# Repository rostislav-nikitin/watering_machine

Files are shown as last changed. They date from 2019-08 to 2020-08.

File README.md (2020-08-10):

# Watering machine

Watering machine is a device that control a watering of the garden. This particular machine provides sequential zones watering. This was made to avoid low watering pressure that can happens in case of the parallel mode zone watering.

This device is a control unit with outputs to the external valves - one per watering zone.

<!--![picture](https://cloud.dynacore.systems/apps/files_sharing/publicpreview/L8qHpaeza94Mbzw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 "") -->


## Modes
The device is designed to work in a two primary modes.

**Normal watering mode**

Used for the regular day-by-day watering. Each zone watering time interval set by the particular zone settings.

**Service mode**

Used for the system blowing before the coservation.
Usually in this mode pump provides an air instead of water. In this case switching to the next zone should be done manually. Through the control button/external input instead of zones watering interval time settings.

According to this, some of button has a different functions depends on the current mode and device state.

## Device logical structure
* [PCB 3D view](#pcb-3d-view "PCB 3D view")
* [Inputs](#Inputs "Inputs")
    * [Power inputs](#power-inputs "Power inputs")
	    * [Main power input](#main-power-input "Main power input")
		    * [Internal low-voltage circuits powering](#internal-low-voltage-circuits-powering "Internal low-voltage circuits powering")
            * [Valves powering](#valves-powering "Valves powering")
        * [Batteries bay](#batteries-bay "Batteries bay")
    * [Logical inputs](#logical-inputs "Logical inputs")
	    * [Control buttons](#control-buttons "Control buttons")
	    * [24 hours internal timer](#24-hours-internal-timer "24 hours internal timer")
	    * [External inputs](#external-inputs)
	        * [External TTL-levels input](#external-ttl-levels-input "External TTL-levels input")
		    * [External rain sensor input](#external-rain-sensor-input "External rain sensor input")
* [Outputs](#outputs "Outputs")
	* [State indicators](#state-indicators "State indicators")
	* [Valves outputs](#valves-outputs "Valves outputs")
	* [Cascading output (not implemented yet)](#cascading-output "Cascading output (not implemented yet)")

## PCB 3D view

<!-- ![picture](https://cloud.dynacore.systems/apps/files_sharing/publicpreview/zAkpRHqrjZDFHtE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 "") -->

	
## Inputs

### Power inputs

#### Main power input

This device can be powered by the 9-36 VAC / 500 mA+ power supply.
Power supply characteristics should be calculated by a next formula:

Power supply voltage = valve voltage. Accepted range: [9 VAC - 36 VAC].

Power supply minimal current = 500 mA (internal circuits) + valve maximal current. Accepterd range: [500 mA - 2 A].

##### Internal low-voltage circuits powering
To power input low-voltage circuits was used primary power supply through current rectification and stabilisation. There is +5 VDC powering used for the low-voltage TTL circuits.
* U = +5 VDC (+/- 5%)
* I <= 700 mA

##### Valves powering
Valves solenoids are powering directly from the [main power input](#main-power-input "Main power input") through triacs without any stabilization or transformation.

#### Batteries bay
Battery powering is consists of the battery bay & controller which control charge level/charge batteries. It powers only chips required to run internal time and store device 24 hours timer state. Because they should be invariant for the external power outages.
Ther was used battery bay for 2x18650 battries. Bacause each battery voltage is 3.8-4.2 VDC. And if they are connected sequetely then they provides ~8 VDC voltage. Which is enough to provide +5 VDC after the stabilization.

### Logical inputs

#### Control buttons
Control buttons should be used to set the current watering mode, zone watering time intervals and change the device state - start, stop watering, switch to the next zone manually.

##### Mode switch button

This button toggle normal watering mode / service mode.

##### Start/Stop/Next button

_In the normal watering mode_

In this mode Start/Stop/Next button works in a Start/Stop toggle mode. When device not in a progress state and rain sensor circuit is disonnected then it start watering. Otherwise if device is in progress then stop.

_In the serivce mode_

In this mode Start/Stop/Next button works in a Start->Next->Stop mode. When watering is stopped then this button starts it in case rain sensor circuit is disconnected. On the next push it switch watering zone to the next one. On push when the last zone is in progress it stops the watering.

##### Timer On/Off switch button

This button toggle [24 hours internal timer](#24-hours-internal-timer "24 hours internal timer") on/off.

##### Zone watering time interwal switch

Each zone watering time can be set with a 3 minutes percision.

There are 2 x 5-position sliding switches per zone. One for the rough setup and one for the fine setup. The total zone watering time interval is a sum of rough and fine values.

_Rough setup 5-position sliding switch_

Positions: [1] - 0 minutes, [2] - 15 minutes, [3] - 30 minutes, [4] - 45 minutes, [5] - 60 minutes

_Fine setup 5-position sliding switch_

Positions: [1] - 0 minutes, [2] - 3 minutes, [3] - 6 minutes, [4] - 9 minutes, [5] - 12 minutes

Example: If rough switch in a position [3] (30 minutes) and fine switch in a position [4] (9 minutes) then zone time interval is equal to the  30 minutes + 9 minutes = 39 minutes

#### 24 hours internal timer
24 hours internal timer is used to start watering each 24 hours with everyday recuring.

Timer On/Off button toggle timer function.

##### Watering start time setup
Watering start time could be setup only in normal watering model. This can be made through a manual start watering by the pressing a start/stop/next or by external TTL-levels input high signal. And after the 24 hours it will starts watering again if device is not in a progress state and rain sensor circuit is disconnected.

#### External inputs

##### External TTL-levels input
The external TTL-levels input behaviour is a same as [Start/Stop/Next button](#start/stop/next-button "Start/Stop/Next button") behaviour. Each high TTL level toggle watering state depends on the current mode and the rain sensor circuit conection state.

##### External rain sensor input
It can be used to connect external rain sensor. Rain sensor shold connect both connector pins on rain begins and disconnect on rain ends. When pins are connected then watering is blocking with a maximal priority - no one signal can start watering.
If it connects pins when watering was is in progress then watering stops. And starts only when next start signal comes in case if rain sensor connector pins will be disconnected. 

## Outputs

### State indicators
* Power indicator: 
    * Off if device powered off
    * On if device is powered on
* Mode indicator: 
    * Off if device is in normal watering mode
    * On if device is in service mode
* In progress indicator:
    * Off if device in suspend mode (waiting for the start watering signal)
    * On if watering is in progress
* Zone watering in progress indicator. Each zone has own it's one:
    * Off if a current zone watering not is in progress state
    * On if a current zone watering is in progress state
* Rain indicator:
    * Off if rain sensor circuit is disconnected
    * On if rain sensor circuit is connected
* Change battery indicator:
    * Off if battery in a good state
    * Flashes if battery is corrupted and need replacement

### Valves outputs
There are ouptuts with [valves powering](#valves-powering "Valves powering"). At the moment only one output is active, according to the current watering zone.

### Cascading output
On last zone watering finish there is raises short high-level TTL impulse to cascade next watering device in watering devices sequence.

## Links
Watering machine intro and description on my YouTube channel:

Watering machine (https://www.youtube.com/playlist?list=PLeO-sYwJtKn6DI-ZfQoCn5SV4Xy-Knc86 "Watering machine")

## Contacts
e-mail: rostislav.nikitin@gmail.com

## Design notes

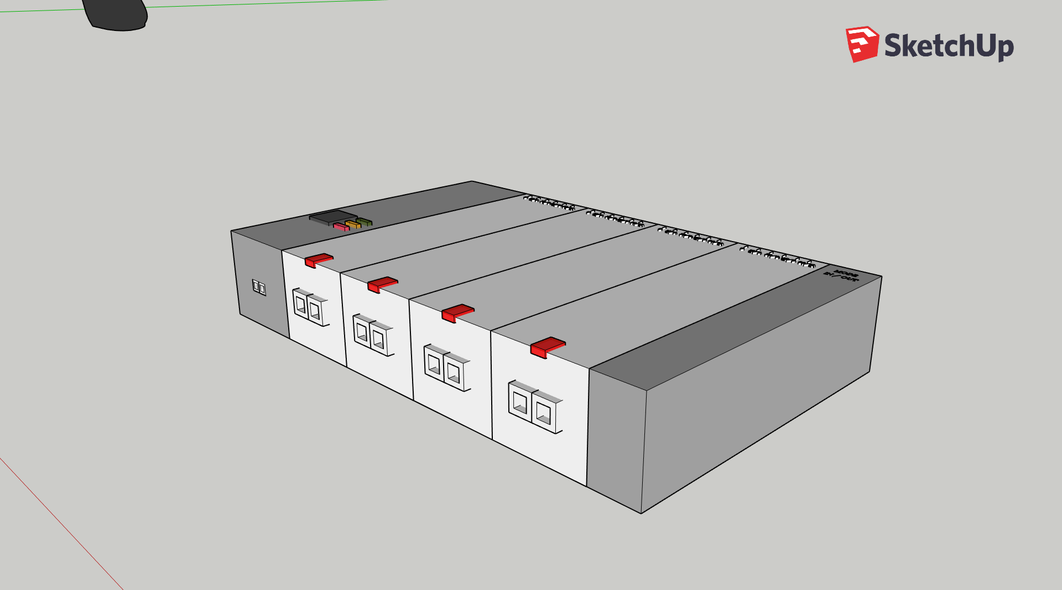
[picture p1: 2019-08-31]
src/case_design/sketches/front-top-right.png

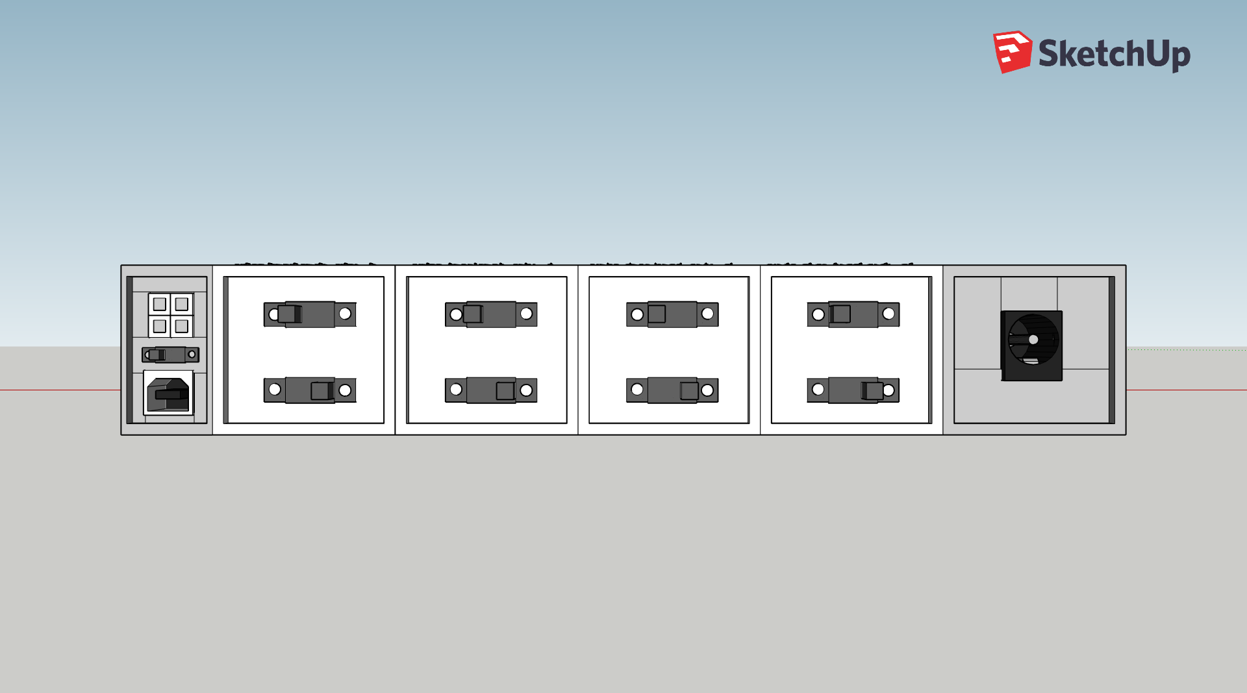
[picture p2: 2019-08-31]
src/case_design/sketches/back.png

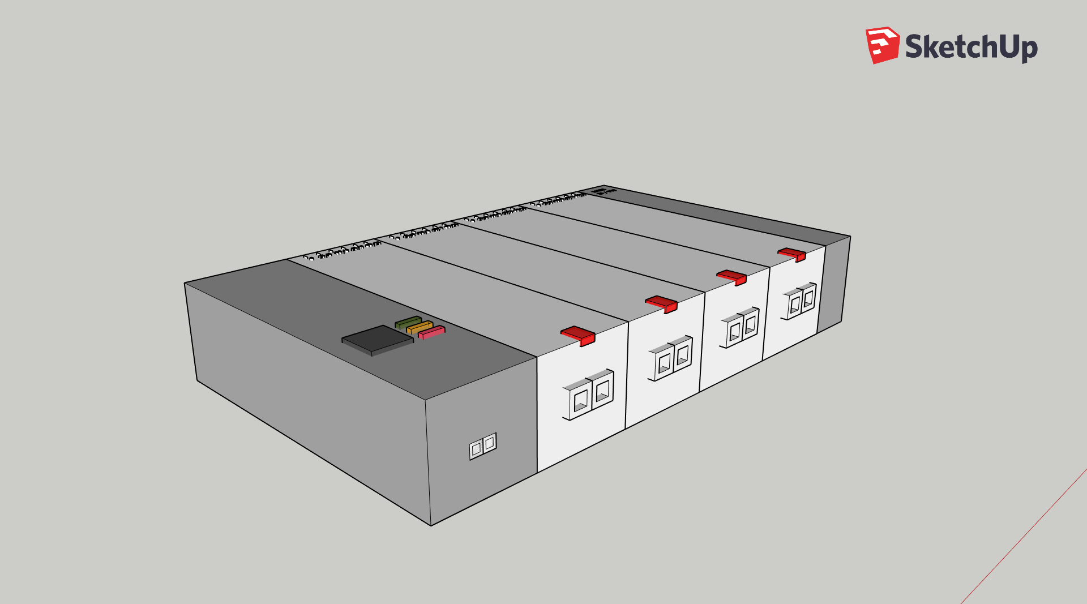
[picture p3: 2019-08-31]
src/case_design/sketches/front-top-left.png

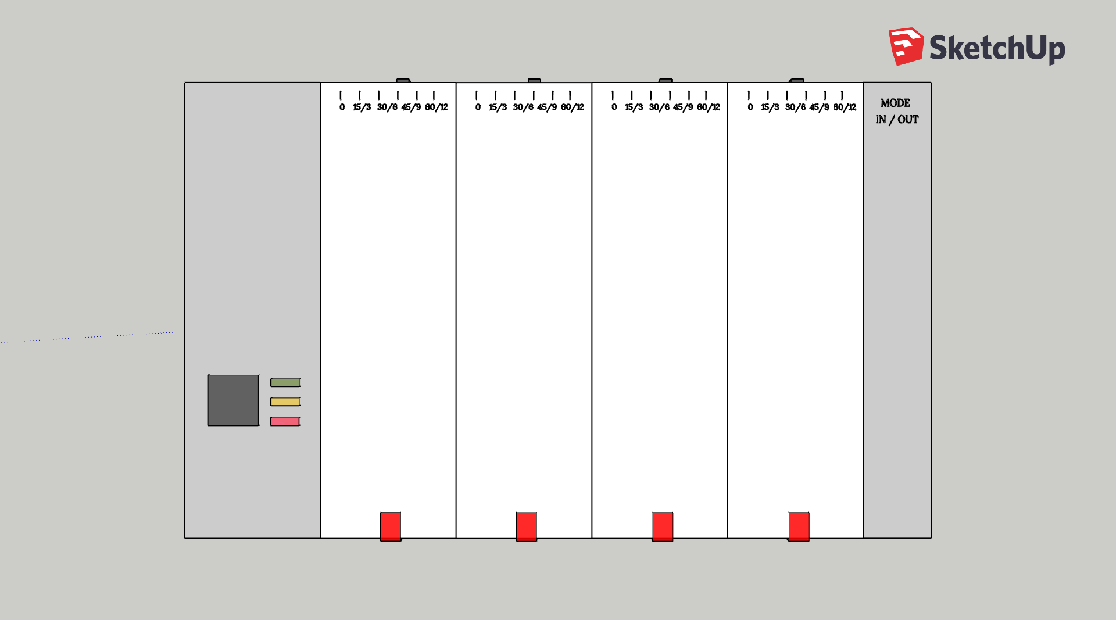
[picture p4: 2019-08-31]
src/case_design/sketches/top.png

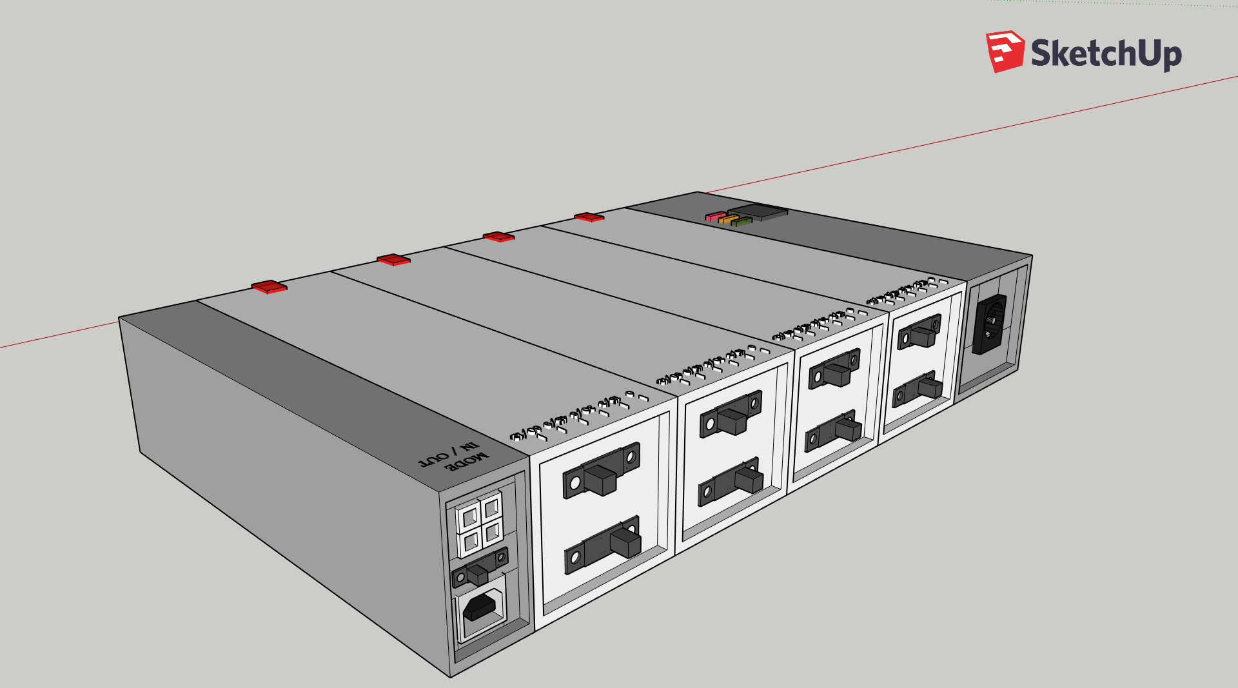
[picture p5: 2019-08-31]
src/case_design/sketches/back-top-left.png

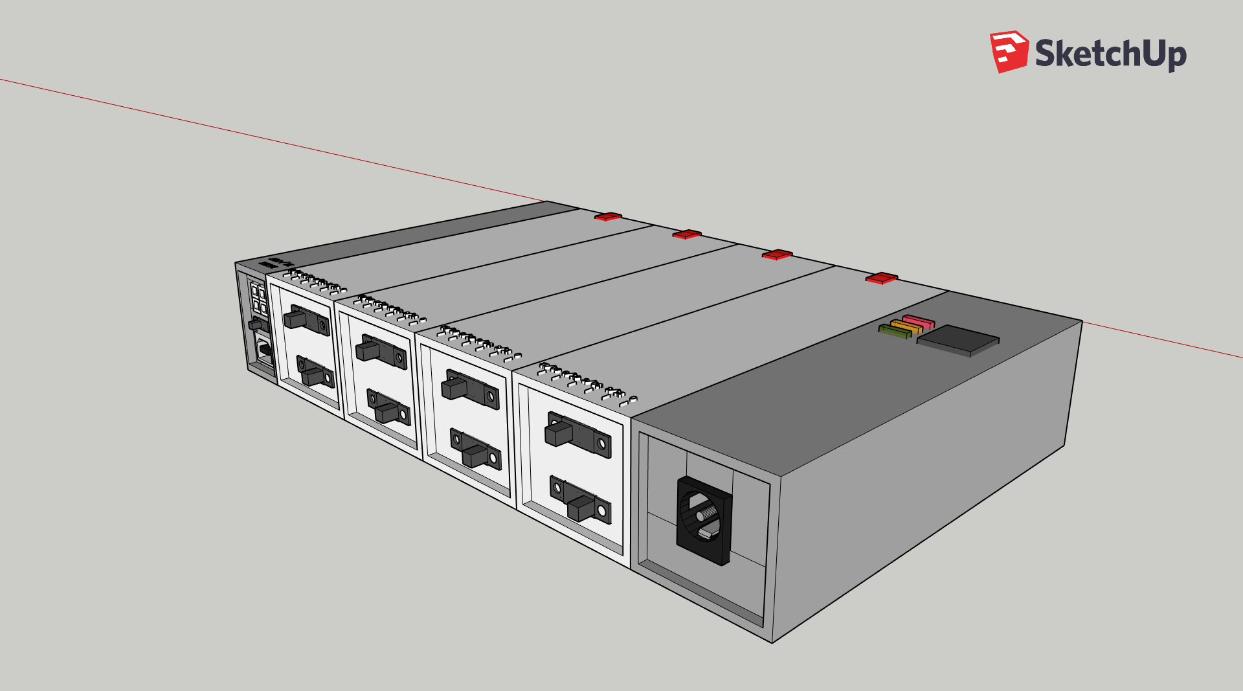
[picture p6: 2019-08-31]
src/case_design/sketches/back-top-right.png

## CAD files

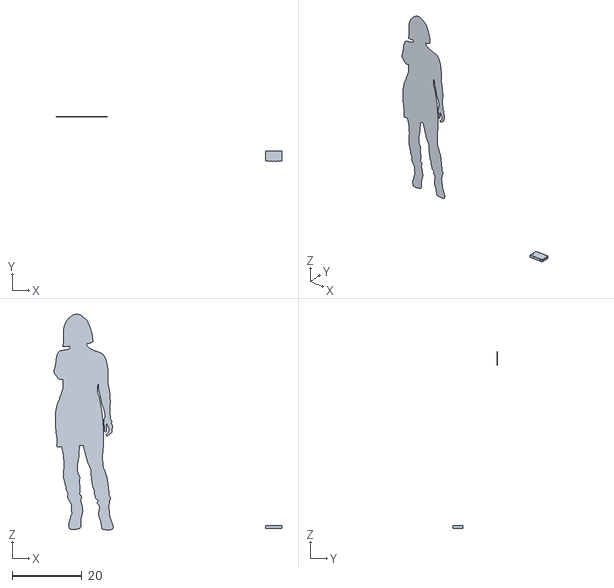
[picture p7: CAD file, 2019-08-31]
src/case_design/case_design.stl
65.6 x 12.9 x 62.1

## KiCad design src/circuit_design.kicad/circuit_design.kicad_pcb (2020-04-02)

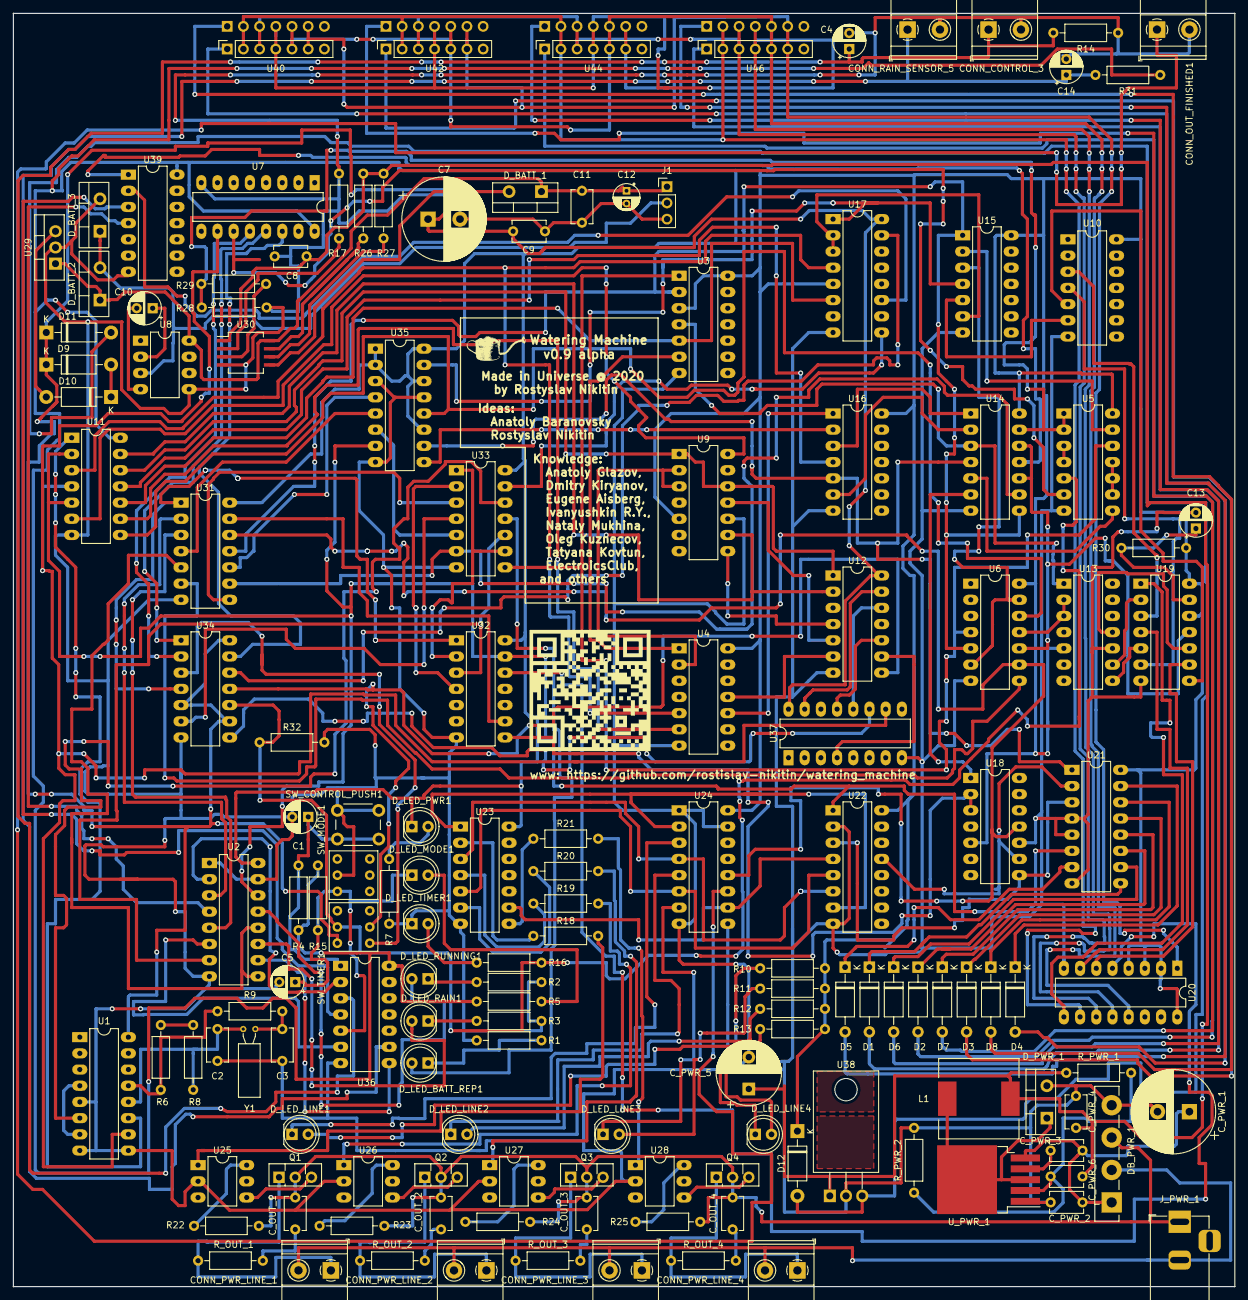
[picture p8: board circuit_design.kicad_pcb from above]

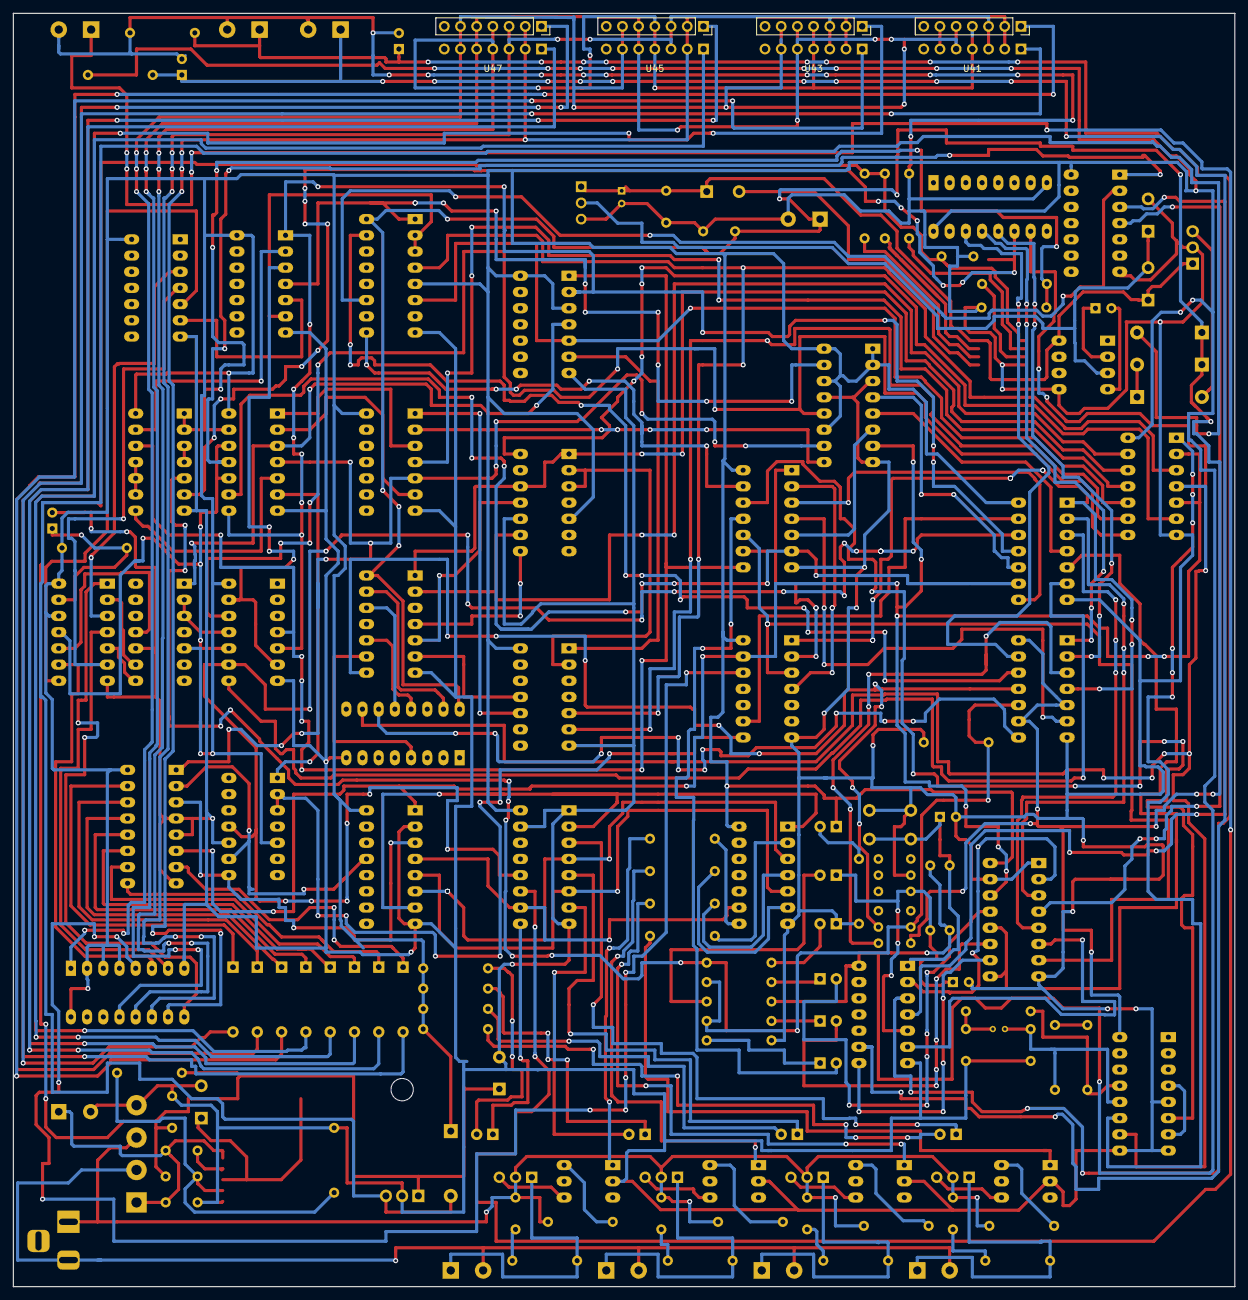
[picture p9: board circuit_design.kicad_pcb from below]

Board: 2 copper layers, 191.5 x 199.6 mm, 154 parts (4 on the bottom side), 186 nets.

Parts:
C1, C4, C5, C13, C14: 100uF; CP_Radial_D5.0mm_P2.50mm
C2: 62pF; C_Disc_D5.1mm_W3.2mm_P5.00mm
C3: 22pF; C_Disc_D5.1mm_W3.2mm_P5.00mm
C7: 1000uF; CP_Radial_D13.0mm_P5.00mm
C8, C11: 100nF; C_Disc_D5.1mm_W3.2mm_P5.00mm
C9: 105; C_Disc_D5.1mm_W3.2mm_P5.00mm
C10: 10uF/16V; CP_Radial_D5.0mm_P2.50mm
C12: 22uF/16V; CP_Radial_D4.0mm_P2.00mm
CONN_CONTROL_3: Conn_01x02_Male; TerminalBlock_Phoenix_MKDS-1,5-2-5.08_1x02_P5.08mm_Horizont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
CONN_OUT_FINISHED1: Conn_01x02_Male; TerminalBlock_Phoenix_MKDS-1,5-2-5.08_1x02_P5.08mm_Horizont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
CONN_PWR_LINE_1, CONN_PWR_LINE_2, CONN_PWR_LINE_3, CONN_PWR_LINE_4: Conn_01x02_Male; TerminalBlock_Phoenix_MKDS-1,5-2-5.08_1x02_P5.08mm_Horizont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
CONN_RAIN_SENSOR_5: Conn_01x02_Male; TerminalBlock_Phoenix_MKDS-1,5-2-5.08_1x02_P5.08mm_Horizont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
C_OUT_1, C_OUT_2, C_OUT_3, C_OUT_4: 103; C_Disc_D5.1mm_W3.2mm_P5.00mm
C_PWR_1: 1000 uF/50V; CP_Radial_D13.0mm_P5.00mm
C_PWR_2, C_PWR_3, C_PWR_4: 105; C_Disc_D5.1mm_W3.2mm_P5.00mm
C_PWR_5: 330 uF/50V; CP_Radial_D10.0mm_P5.00mm
C_PWR_6: 333; C_Disc_D5.1mm_W3.2mm_P5.00mm
D1, D2, D3, D4, D5, D6, D7, D8: 1N5817; D_A-405_P10.16mm_Horizontal
D9, D11, D12: 1N4007; D_DO-41_SOD81_P10.16mm_Horizontal
D10: 1N5817; D_DO-41_SOD81_P10.16mm_Horizontal
DB_PWR_1: RS207; Diode_Bridge_Vishay_GBL
D_BATT_1, D_BATT_2, D_BATT_3: SS24T3G; TO-220-2_Vertical
D_LED_BATT_REP1: LED; LED_D5.0mm
D_LED_LINE1, D_LED_LINE2, D_LED_LINE3, D_LED_LINE4: LED; LED_D5.0mm
D_LED_MODE1: LED; LED_D5.0mm
D_LED_PWR1: LED; LED_D5.0mm
D_LED_RAIN1: LED; LED_D5.0mm
D_LED_RUNNING1: LED; LED_D5.0mm
D_LED_TIMER1: LED; LED_D5.0mm
D_PWR_1: MBR745; TO-220-2_Vertical
J1: CONN_BAT; PinHeader_1x03_P2.54mm_Vertical
J_PWR_1: Barrel_Jack; BarrelJack_Horizontal
L1: 47 uH/5A; L_12x12mm_H6mm
Q1, Q2, Q3, Q4: BT134-600E; TO-126-3_Vertical
R1: 200; R_Axial_DIN0207_L6.3mm_D2.5mm_P10.16mm_Horizontal
R2, R3, R5, R7, R10, R11, R12, R13: 270Ohm; R_Axial_DIN0207_L6.3mm_D2.5mm_P10.16mm_Horizontal
R4, R14, R15, R22, R23, R24, R25, R31: 1KOhm; R_Axial_DIN0207_L6.3mm_D2.5mm_P10.16mm_Horizontal
R6, R8: 10MOhm; R_Axial_DIN0207_L6.3mm_D2.5mm_P10.16mm_Horizontal
R9: 510KOhm; R_Axial_DIN0207_L6.3mm_D2.5mm_P10.16mm_Horizontal
R16: 270; R_Axial_DIN0207_L6.3mm_D2.5mm_P10.16mm_Horizontal
R17, R27, R30: 10K; R_Axial_DIN0207_L6.3mm_D2.5mm_P10.16mm_Horizontal
R18, R19, R20, R21: 100 Ohm; R_Axial_DIN0207_L6.3mm_D2.5mm_P10.16mm_Horizontal
R26: 0.5R; R_Axial_DIN0207_L6.3mm_D2.5mm_P10.16mm_Horizontal
R28: 500R; R_Axial_DIN0207_L6.3mm_D2.5mm_P10.16mm_Horizontal
R29: 400R; R_Axial_DIN0207_L6.3mm_D2.5mm_P10.16mm_Horizontal
R32: 1 KOhm; R_Axial_DIN0207_L6.3mm_D2.5mm_P10.16mm_Horizontal
R_OUT_1, R_OUT_2, R_OUT_3, R_OUT_4: 39; R_Axial_DIN0207_L6.3mm_D2.5mm_P10.16mm_Horizontal
R_PWR_1: 15K; R_Axial_DIN0207_L6.3mm_D2.5mm_P10.16mm_Horizontal
R_PWR_2: 2.4 K; R_Axial_DIN0207_L6.3mm_D2.5mm_P10.16mm_Horizontal
SW_CONTROL_PUSH1: SW_DPST_x2; SW_PUSH_6mm
SW_MODE1: SW_DPDT_x2; PB22E09
SW_TIMER1: SW_DPDT_x2; PB22E09
U1: К176ИЕ12; DIP-16_W7.62mm_LongPads
U2, U24: К155ЛП10; DIP-16_W7.62mm_LongPads
U3: К155ЛЕ3; DIP-14_W7.62mm_LongPads
U4, U15, U23, U32, U39: К155ЛН1; DIP-14_W7.62mm_LongPads
U5: К155ЛА3; DIP-14_W7.62mm_LongPads
U6, U14: К155ЛЛ1; DIP-14_W7.62mm_LongPads
U7, U37: 4020; DIP-16_W7.62mm_LongPads
U8: ICL7660; DIP-8_W7.62mm_LongPads
U9, U13, U18: К155ИЕ5; DIP-14_W7.62mm_LongPads
U10, U34: К155ЛА4; DIP-14_W7.62mm_LongPads
U11, U16, U33: К155ЛИ1; DIP-14_W7.62mm_LongPads
U12: К155ЛА1; DIP-14_W7.62mm_LongPads
U17, U35: К155ТВ15; DIP-16_W7.62mm_LongPads
U19: К155ЛП5; DIP-14_W7.62mm_LongPads
U20: К155ИВ1; DIP-16_W7.62mm_LongPads
U21: К155ИД7; DIP-16_W7.62mm_LongPads
U22: К155ИД4; DIP-16_W7.62mm_LongPads
U25, U26, U27, U28: MOC3062M; DIP-6_W7.62mm_LongPads
U29: LM7806_TO220; TO-220-3_Vertical
U30: SC6038; SO-8_5.3x6.2mm_P1.27mm
U31: К155ЛЕ1; DIP-14_W7.62mm_LongPads
U36: К155ТЛ2; DIP-14_W7.62mm_LongPads
U38: LM7806_TO220; TO-220-3_Horizontal_TabDown
U40, U41, U42, U43, U44, U45, U46, U47: SPFT_Sliding_Switch; PinSocket_1x07_P2.54mm_Vertical
U_PWR_1: XL4015; TO-263-5_TabPin3
Y1: 32768; Crystal_C38-LF_D3.0mm_L8.0mm_Horizontal

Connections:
+5V: D12.1, D_LED_PWR1.1, R4.1, R5.1, R10.2, R11.2, R12.2, R13.2, R15.1, R30.1, R31.1, U2.16, U3.3, U3.14, U4.14, U5.14, U6.14, U7.16, U9.5, U10.14, U11.14, U13.5, U14.14, U15.14, U16.14, U17.5, U18.5, U19.12, U19.14, U20.2, U20.3, U20.4, U20.16, U21.16, U22.16, U23.14, U24.16, U31.14, U32.14, U33.14, U35.1, U35.2, U35.11, U35.14, U35.16, U36.14, U39.14
+9V: C8.1, C_PWR_4.1, C_PWR_5.1, C_PWR_6.1, L1.2, R26.1, R27.1, R_PWR_1.1, U30.1, U38.1
/Comparison.Equal: U15.6, U17.2, U17.3
/Completed(In): U6.8, U31.6
/Conn_Control_Raw: C4.1, CONN_CONTROL_3.1, R14.1, U36.3
/Control(Ext.2): U2.4, U39.4
/Control(Ext.): U2.2, U36.2
/Control(In1): U2.3, U31.2
/Control(In2): U2.5, U31.3
/D0: U20.10, U40.2, U41.2, U42.2, U43.2, U44.2, U45.2, U46.2, U47.2
/D1: U20.11, U40.3, U41.3, U42.3, U43.3, U44.3, U45.3, U46.3, U47.3
/D2: U20.12, U40.4, U41.4, U42.4, U43.4, U44.4, U45.4, U46.4, U47.4
/D3: U20.13, U40.5, U41.5, U42.5, U43.5, U44.5, U45.5, U46.5, U47.5
/D4: U20.1, U40.6, U41.6, U42.6, U43.6, U44.6, U45.6, U46.6, U47.6
/Mem.Comparison.Equal: U3.5, U11.10, U17.6
/Mode(Ext.): U2.6, U36.6
/Mode(In): U2.7, U32.3, U33.10
/Mode_Raw: C5.1, D_LED_MODE1.1, R15.2, SW_MODE1.3, U36.5
/Next(Out): U3.1, U5.12, U6.4, U33.8
/Rain(In): U2.9, U2.12, U31.5
/Rain(Led): D_LED_RAIN1.2, U2.11
/Rain_Sensor(Ext.): U2.10, U36.8
/Rain_Sensor_Raw: C14.1, CONN_RAIN_SENSOR_5.1, R31.2, U36.9
/Reset(Out): U3.2, U6.5, U14.8, U15.1, U31.11
/Running(Led): D_LED_RUNNING1.2, U2.13
/Running(Out): U2.14, U11.2, U11.5, U21.6, U22.1, U32.13, U35.7
/RunningInv(out): U20.5, U32.12
/Timer.End: U3.4, U13.1, U14.3
BATT_OUT_+: C11.1, C12.1, D_BATT_1.1, D_BATT_2.1, J1.1, U8.8, U29.1, U30.8
BATT_OUT_MID: D_BATT_2.2, D_BATT_3.1, J1.2, U8.3
CLK_MIN: U1.10, U7.10, U11.4, U37.10
CLK_SEC: U1.6, U33.12
Finished: U6.9, U18.11, U24.12, U31.12
GND: C1.2, C2.2, C3.2, C4.2, C5.2, C7.2, C8.2, C9.2, C11.2, C12.2, C13.2, C14.2, CONN_CONTROL_3.2, CONN_OUT_FINISHED1.2, CONN_RAIN_SENSOR_5.2, C_PWR_1.2, C_PWR_2.2, C_PWR_4.2, C_PWR_5.2, DB_PWR_1.4, D_BATT_3.2, D_LED_TIMER1.1, D_PWR_1.2, J1.3, R1.1, R2.2, R3.2, R7.2, R14.2, R17.2, R28.1, R32.2, R_PWR_2.2, SW_CONTROL_PUSH1.1, SW_MODE1.2, U1.5, U1.8, U1.9, U2.1, U2.8, U2.15, U3.7, U4.7, U5.7, U6.7, U7.8, U8.5, U9.10, U10.7, U11.7, U12.7, U13.10, U14.7, U15.7, U16.7, U17.8, U18.10, U19.7, U20.8, U21.4, U21.5, U21.8, U22.2, U22.8, U23.7, U24.1, U24.8, U24.15, U25.2, U26.2, U27.2, U28.2, U29.2, U30.4, U31.7, U32.7, U33.7, U34.7, U35.3, U35.8, U35.13, U36.7, U37.8, U38.2, U39.7, U_PWR_1.1
GNDREF: CONN_PWR_LINE_1.2, CONN_PWR_LINE_2.2, CONN_PWR_LINE_3.2, CONN_PWR_LINE_4.2, DB_PWR_1.2, J_PWR_1.2
Init: U6.10, U14.10, U14.12, U19.11
unnamed: C1.1, R4.2, SW_CONTROL_PUSH1.2, U36.1
unnamed: C2.1, R8.2, U1.12, Y1.1
unnamed: C3.1, R9.1, Y1.2
unnamed: C10.1, U8.2
unnamed: C10.2, U8.4
unnamed: C13.1, R30.2, U19.13
unnamed: CONN_OUT_FINISHED1.1, U24.11
unnamed: CONN_PWR_LINE_1.1, Q1.1, R_OUT_1.2
unnamed: CONN_PWR_LINE_2.1, Q2.1, R_OUT_2.2
unnamed: CONN_PWR_LINE_3.1, Q3.1, R_OUT_3.2
unnamed: CONN_PWR_LINE_4.1, Q4.1, R_OUT_4.2
unnamed: C_OUT_1.2, R_OUT_1.1
unnamed: C_OUT_2.2, R_OUT_2.1
unnamed: C_OUT_3.2, R_OUT_3.1
unnamed: C_OUT_4.2, R_OUT_4.1
unnamed: C_PWR_1.1, C_PWR_2.1, C_PWR_3.1, DB_PWR_1.1, U_PWR_1.5
unnamed: C_PWR_3.2, U_PWR_1.4
unnamed: C_PWR_6.2, R_PWR_1.2, R_PWR_2.1, U_PWR_1.2
unnamed: D1.1, U21.9
unnamed: D1.2, U46.1
unnamed: D2.1, U21.11
unnamed: D2.2, U44.1
unnamed: D3.1, U21.13
unnamed: D3.2, U42.1
unnamed: D4.1, U21.15
unnamed: D4.2, U40.1
unnamed: D5.1, U21.7
unnamed: D5.2, U47.1
unnamed: D6.1, U21.10
unnamed: D6.2, U45.1
unnamed: D7.1, U21.12
unnamed: D7.2, U43.1
unnamed: D8.1, U21.14
unnamed: D8.2, U41.1
unnamed: D9.2, D10.1
unnamed: D10.2, U29.3
unnamed: D11.2, D12.2, U38.3
unnamed: D_BATT_1.2, U30.5
unnamed: D_LED_BATT_REP1.1, R1.2
unnamed: D_LED_BATT_REP1.2, U33.11
unnamed: D_LED_LINE1.1, U24.3
unnamed: D_LED_LINE1.2, R13.1
unnamed: D_LED_LINE2.1, U24.5
unnamed: D_LED_LINE2.2, R12.1
unnamed: D_LED_LINE3.1, U24.7
unnamed: D_LED_LINE3.2, R11.1
unnamed: D_LED_LINE4.1, U24.9
unnamed: D_LED_LINE4.2, R10.1
unnamed: D_LED_MODE1.2, R5.2
unnamed: D_LED_PWR1.2, R7.1
unnamed: D_LED_RAIN1.1, R3.1
unnamed: D_LED_RUNNING1.1, R2.1
unnamed: D_LED_TIMER1.2, R16.2
unnamed: D_PWR_1.1, L1.1, U_PWR_1.3
unnamed: Q1.3, U25.4
unnamed: Q2.3, U26.4
unnamed: Q3.3, U27.4
unnamed: Q4.3, U28.4
unnamed: R6.1, R9.2, U1.13
unnamed: R6.2, R8.1
unnamed: R16.1, R32.1, SW_TIMER1.2, U5.5, U34.10
unnamed: R17.1, U30.2
unnamed: R18.1, U23.2
unnamed: R18.2, U25.1
unnamed: R19.1, U23.4
unnamed: R19.2, U26.1
unnamed: R20.1, U23.6
unnamed: R20.2, U27.1
unnamed: R21.1, U23.8
unnamed: R21.2, U28.1
unnamed: R22.1, U25.6
unnamed: R23.1, U26.6
unnamed: R24.1, U27.6
unnamed: R25.1, U28.6
unnamed: R26.2, U30.7
unnamed: R27.2, U30.6
unnamed: R28.2, R29.1, U5.1, U5.2, U14.13
unnamed: R29.2, U30.3
unnamed: SW_TIMER1.5, U12.8, U34.11
unnamed: SW_TIMER1.6, U34.3
unnamed: U1.4, U1.7
unnamed: U1.11, U11.1
unnamed: U3.6, U4.1
unnamed: U4.2, U9.2, U9.3
unnamed: U5.3, U5.4
unnamed: U5.6, U7.11
unnamed: U5.9, U5.10, U5.11
unnamed: U10.3, U19.3
unnamed: U10.4, U19.6
unnamed: U10.5, U19.8
unnamed: U10.6, U15.5
unnamed: U4.5, U11.3, U17.4
unnamed: U9.14, U11.6
unnamed: U6.12, U11.8, U35.12
unnamed: U4.6, U11.9
unnamed: U11.11, U16.4
unnamed: U9.1, U9.12, U11.12, U12.1
unnamed: U9.9, U11.13, U12.2
unnamed: U9.8, U12.4
unnamed: U9.11, U12.5
unnamed: U4.11, U12.6
unnamed: U12.9, U37.4
unnamed: U12.10, U37.13
unnamed: U12.12, U37.12
unnamed: U12.13, U37.15
unnamed: U6.11, U13.2, U13.3
unnamed: U13.8, U19.5
unnamed: U13.9, U19.2
unnamed: U13.11, U19.10
unnamed: U14.1, U16.3
unnamed: U14.2, U16.6
unnamed: U14.4, U16.5, U21.1, U35.10
unnamed: U5.8, U14.5
unnamed: U14.6, U18.1
unnamed: U14.9, U31.9, U33.6
unnamed: U14.11, U39.1
unnamed: U5.13, U15.2
unnamed: U6.6, U6.13, U15.3
unnamed: U15.4, U17.1, U35.15
unnamed: U4.10, U16.1
unnamed: U16.2, U35.9
unnamed: U17.9, U33.13
unnamed: U17.11, U39.2
unnamed: U17.15, U34.12
unnamed: U18.2, U18.3, U32.8
unnamed: U18.8, U21.3, U22.3
unnamed: U18.9, U21.2, U22.13
unnamed: U19.1, U20.9
unnamed: U19.4, U20.7
unnamed: U19.9, U20.6
unnamed: U22.4, U23.9, U24.10
unnamed: U22.5, U23.5, U24.6
unnamed: U22.6, U23.3, U24.4
unnamed: U22.7, U23.1, U24.2
unnamed: U31.1, U32.1, U34.4
unnamed: U31.4, U35.5
unnamed: U31.8, U33.3
unnamed: U31.10, U35.4
unnamed: U31.13, U32.9
unnamed: U32.2, U33.1, U33.9
unnamed: U32.4, U33.2
unnamed: U33.4, U34.6
unnamed: U33.5, U35.6
unnamed: U7.13, U34.1
unnamed: U7.12, U34.2
unnamed: U34.8, U37.11
unnamed: U7.14, U34.13
unnamed: U36.4, U39.3
PWR_ALW: C7.1, C9.1, D9.1, D11.1, SW_TIMER1.3, U1.16, U12.14, U17.16, U34.5, U34.9, U34.14, U37.16
VAC: C_OUT_1.1, C_OUT_2.1, C_OUT_3.1, C_OUT_4.1, DB_PWR_1.3, J_PWR_1.1, Q1.2, Q2.2, Q3.2, Q4.2, R22.2, R23.2, R24.2, R25.2

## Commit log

2019-08-31 Initial commit. Was created a next sections: 01. Documentation. Requirements 02. Documentation. User Manual 03. Case design 04. Digital design (KTechLab) 05. Circuit design (KiCAD 5.X)
    [circuit_design-B.Cu.gbr, circuit_design-B.Mask.gbr, circuit_design-B.Paste.gbr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]
2019-08-31 Sketches & STL model was added to the case design.
    [case_design.stl]
2019-10-03 01. Fixed but with triggers: 1. U35A, U35B: the ^K was reconnected from the +VCC to the GND 2. U17A: the ^K was reconnected without inverter 3. U35B, U17A: the ^R was reconnected with inversion 02. R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
    [circuit_design.sch]
2019-10-03 01. The contacts bounce was fixed (the Shmitt trigger was added) 02. U35A JK-trigger outputs was inverted (to solve power on trigger default true state)
    [circuit_design.sch]
2019-10-23 01. The dynacore lib was updated 01. The К176ИЕ13 element was added 02. The circuit desaign was updated 01. The 24 hours re-start loop module was implemented
    [circuit_design.sch]
2019-10-23 01. The circuit design was updated 01. All the elements was moved inside an accepted area
    [circuit_design.sch]
2019-10-23 01. The circuit design was updated - The 24-hours timer reset was fixed
    [circuit_design.sch]
2019-10-23 01. The circuit design was updated - The 24-hours timer switch was replaced with the connectors
    [circuit_design.sch]
2019-10-24 The circuit design was updated - The +5V USB powering was replaced with the +24V LM317 based powering
    [circuit_design.sch]
2019-10-25 The powering module was updated - The resistors values was updated to provide more stable voltage
    [circuit_design.sch]
2019-10-26 The circuit design was updated - The open-collector output inverted (К155ЛН3) was replace with simple inverter one (К155ЛН1) - The logic powering was update to support AC/DC input voltage (diode brid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
    [circuit_design.sch]
2019-10-28 The circuit design was updated - The capicator and GNDREF was added to the powering module
    [circuit_design.sch]
2019-10-29 The circuit design was updated - The timer reset logic was updated. Now timer resets on watering start instead on button was pressed.
    [circuit_design.sch]
2019-10-29 The circuit design was updated: - Now timer resets on washing starting and button is pressed (to avoid overwrite timer by external source).
    [circuit_design.sch]
2019-11-02 01. The state machine was updated - Reset on complete was switched off. As result the circuit started to work correctly and it design was simplified 02. The 24-hours timer was updated - Push button w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
    [circuit_design.sch]
2019-11-08 01. 24h timer module was fixed. Now on 24h event it circuit already in the 'running' is does not stopping 02. U18 reset was fixed 03. High voltage module (with opto and simple triacs) was added 04. C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
    [circuit_design.sch]
2019-11-15 01. Power module was updated - Main chip was changed from the LM317 to the XL4015 - XLSEMI library was added
    [circuit_design.sch]
2019-11-15 The RC chain was added to the triac high voltage outputs.
    [circuit_design.sch]
2019-11-16 01. CLK connection was changed to release mode (run at 1 KHz instead of 1 Hz) 02. Added inputs filtering capicators
    [circuit_design.sch]
2019-11-16 The output triacs filters components was updated
    [circuit_design.sch]
2019-11-16 Small fixes was made
    [circuit_design.sch]
2019-11-16 Power module was fixed: - Missing drossel was added
    [circuit_design.sch]
2019-11-16 The chip footprint was fixed: - The socket was replaced with header
    [circuit_design.kicad_pcb, circuit_design.sch]
2019-11-18 The RTC was updated: - The RTC power supply/battery switch was added (to avoid RTC reset on power off) - The capicators was added to the RTC chips power pins (to avoid RTC reset on switching from the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
    [circuit_design.sch]
2019-11-18 01. The Digikey library was added 02. The RTC power supply/battery switch was updated - The battery holder was updated to the Digikey BS-7 one
    [circuit_design.sch]
2019-11-18 01. The dynacore library was update: - The AOP605 P-N channel MOSFETs DIP8 element was added - Some element(s) was refactored 02. The RTC power supply/battery switch was updated: - The two p-channel 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
    [circuit_design.sch]
2019-11-22 Battery support was added
    [circuit_design.sch]
2019-11-23 The power supply was updated: - The voltage was changed to the +9V - The LM0805 was added
    The power supply / battery swith updated:
    - The schema was redesigned
    - The simple batterys was replaced with the rechargable ones
    - The charging controller and the balancer was added
    [circuit_design.sch]
2019-11-23 The circuit design was annotated
    [circuit_design.sch]
2019-11-24 The restricting diode (to avoid battery current cover all the schema) was added.
    [circuit_design.sch]
2019-11-24 Added paraller power supply ~+5V output through diode to the whole circuit.
    [circuit_design.sch]
2019-12-02 01. The small refactoring was done 02. The on-power init by reset module was added
    [circuit_design.kicad_pcb, circuit_design.sch]
2019-12-02 The diode bridge was updated
    [circuit_design.sch]
2019-12-03 01. Some of chips was updated to ones without common VCC to fix common powerting issue. 02. The PCB layout update was started
    [circuit_design.kicad_pcb, circuit_design.sch]
2019-12-05 The PCB layout was updated: - AC circuit was located
    [circuit_design.kicad_pcb, circuit_design.sch]
2019-12-06 The PCB layout was updated: - The battery module was updated
    [circuit_design.kicad_pcb]
2019-12-07 The PCB layout was updated
    [circuit_design.kicad_pcb]
2019-12-10 The PCB layout was fixed according to the rules.
    [circuit_design.kicad_pcb, circuit_design.sch]
2019-12-26 01. The PCB layout was updated 02. The gerber files was updated 03. The README.md was initialized
    [circuit_design-B.Cu.gbr, circuit_design-B.Mask.gbr, circuit_design-B.Paste.gbr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]
2019-12-26 The README.md file was updated: - The PCB 3D layout was added
    [circuit_design.kicad_pcb]
2020-02-22 01. The "Init" signal label was added 02. The "Init" signal was used to reset the running state and the battery timer triggers 03. Shmidt triggers was added to the Control(Ext.2) and Mode(Ext.) inputs
    [circuit_design.kicad_pcb, circuit_design.sch]
2020-02-22 The "Init" time was increased to x10 times - The "Init" module resistor was updated from the 1K to the 10K
    [circuit_design.sch]
2020-02-24 The Control(Ext.2) input was updated to output by default a "0" signal and accept a TTL input signal: - The inverter between the Shmidt trigger and the Control(Ext.2) was added - The resistor was con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
    [circuit_design.sch]
2020-02-25 The 1N4007 D1-D7 rectifier diodes was changed to the 1N5817 Shottkey ones.
    [circuit_design.sch]
2020-02-26 01. The connectors was placed to the external signals near to chips (to avoid long lines) 02. The LM7806(U38) was put to the board to dissipate heat
    [circuit_design.kicad_pcb, circuit_design.sch]
2020-02-28 01. The BT136-600E triacs was replaced with the BT134-600E ones 02. The SMD drossel (L=47uH/0.88A) was replaced with the (L=47uH/2.5A) one 03. The board dimensions was decreased: - Width: 220.345 -> 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
    [circuit_design.kicad_pcb, circuit_design.sch]
2020-02-28 The PCB layout was optimized
    [circuit_design.kicad_pcb]
2020-02-28 The 24-hours timer JCONN_SW_DPST02_TIMER_1 connector placement was changed (to be much more far from the other inputs).
    [circuit_design.kicad_pcb]
2020-02-28 The labels was updated: - Was placed outside of the parts - Was situated to be more readable
    [circuit_design.kicad_pcb, circuit_design.sch]
2020-02-28 The git repository URI and the corresponding QR code was added to the silkography layer.
    [circuit_design.kicad_pcb]
2020-02-28 The QR code footprint was locked.
    [circuit_design.kicad_pcb]
2020-02-29 The board size was reduced to the 198.755 mm x 170.815 mm
    [circuit_design.kicad_pcb]
2020-02-29 Unnecessary elements was removed.
    [circuit_design.kicad_pcb]
2020-02-29 The PCB layout was updated from the schematic.
    [circuit_design.kicad_pcb]
2020-02-29 01. The unnecessary element was removed 02. The QR code was added
    [circuit_design.kicad_pcb]
2020-03-05 The timer reset logic was updated. Now it is resetting not by the start button/external signal but on enabed.
    [circuit_design.kicad_pcb, circuit_design.sch]
2020-03-18 PCB layout was updated
    [circuit_design.kicad_pcb, circuit_design.sch]
2020-03-19 01. The power module was moved bottom 02. The zone time select jumpers was replaced with sliding switches 03. The zone time select module was moved top 04. The 24-hour timer LED circuit was added
    [circuit_design.kicad_pcb, circuit_design.sch]
2020-03-20 The PCB was updated to be compartible with KRADEX Z26 box 01. Connectors was replaced with buttons, LEDs and terminal blocks 02. Buttons, LEDs and terminal blocks positioning was updated Out finish s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
    [circuit_design.kicad_pcb, circuit_design.sch]
2020-03-21 01. The labels positions was updated 02. The diode bridge footprint was updated 03. The drill holes was added/updated
    [_saved_circuit_design.sch, circuit_design.kicad_pcb]
2020-03-21 The back/front mask was removed from the sliding switches holes.
    [circuit_design.kicad_pcb]
2020-03-21 The high capicator(s) position was updated to create possibility to put them vertically.
    [_saved_circuit_design.sch, circuit_design.kicad_pcb, circuit_design.sch]
2020-03-21 The battery health check watchdog enabling jumper was added. Now device can be configured to use a battery health check watchdog or not.
    [circuit_design.kicad_pcb, circuit_design.sch]
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2020-03-22 The battery health check jumper was replaced with a signal from the 24-hours timer on/off button. Now used a next battery health check enabling algorithm: If 24-hours timer is in "on" state then the 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
    [circuit_design.kicad_pcb, circuit_design.sch]
2020-03-22 01. The knowledge people list was updated: Eugene Aisberg was added 02. The labels positions was updated
    [circuit_design.kicad_pcb]
2020-04-01 The gerber/drill files was updated.
    [circuit_design-B.Cu.gbr, circuit_design-B.Mask.gbr, circuit_design-B.Paste.gbr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]
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
